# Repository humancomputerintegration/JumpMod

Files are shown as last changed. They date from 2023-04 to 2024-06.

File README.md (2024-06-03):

# JumpMod: Haptic Backpack that Modifies Users’ Perceived Jump

This is the repository for PCB schematics, Arduino code and hardware design files used to build the haptic backpack the "JumpMod: Haptic Backpack that Modifies Users’ Perceived Jump" paper (ACM CHI2023) by Romain Nith, Jacob Serfaty, Samuel Shatzkin, Alan Shen, and Pedro Lopes.

For more information, please refer to our paper: http://lab.plopes.org/#JumpMod

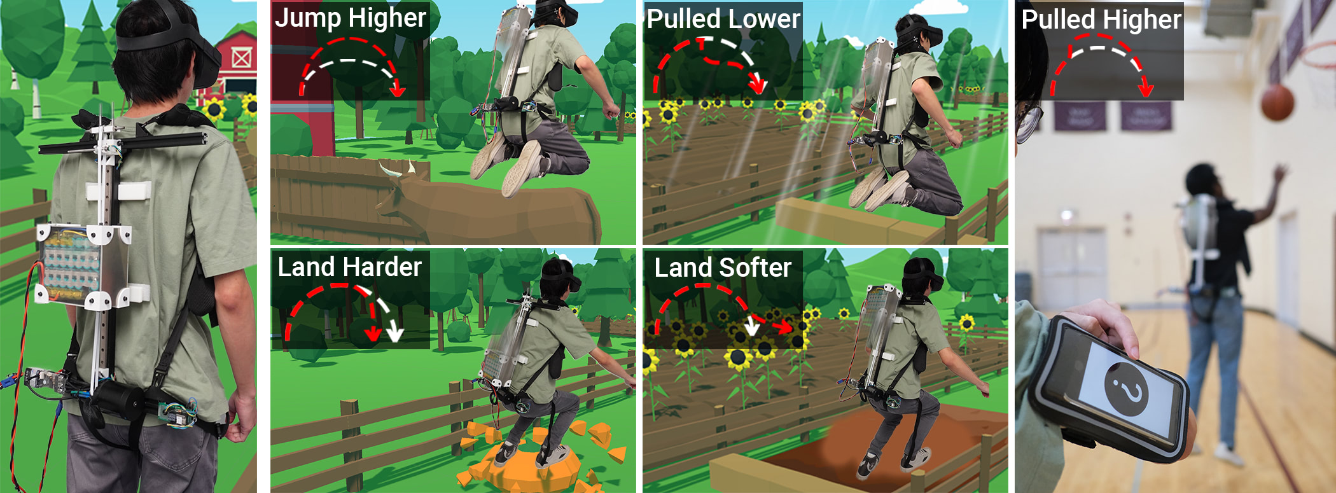
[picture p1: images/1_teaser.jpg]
1_teaser


# parts for each assembly

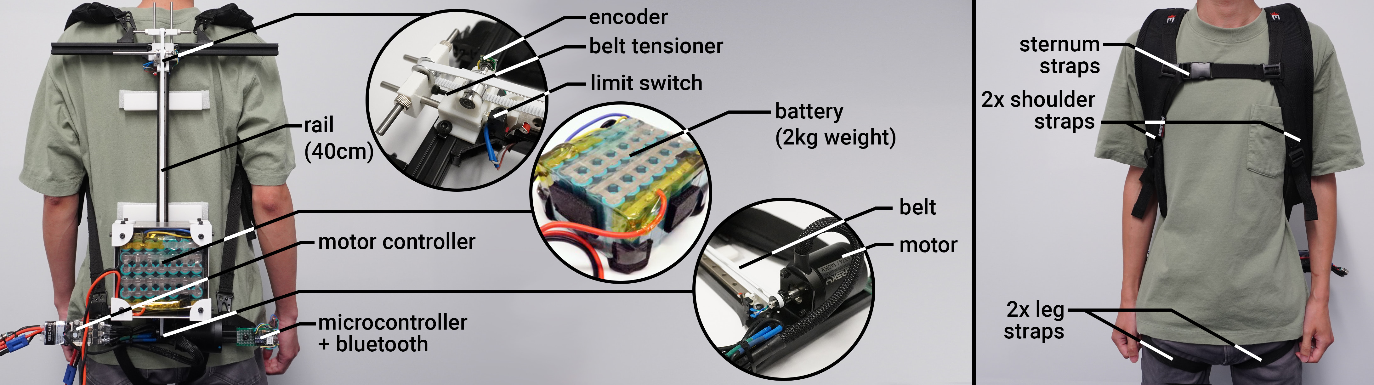
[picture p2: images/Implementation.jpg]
Implementation


| **Item** | **Qty** | **Exemplary link** | **Approx. unit cost (in USD)** |
| --- | --- | --- | --- |
| **Mechanical Frame** |
| 400mm extrusion aluminum | 2 | [Amazon link](https://www.amazon.com/gp/product/B08Y8N7FD1/ref=ppx_yo_dt_b_search_asin_title?ie=UTF8&psc=1) | 4.75 |
| 480mm extrusion aluminum | 1 | [Amazon link](https://www.amazon.com/Coavoo-Aluminum-Extrusion-Extruded-Profiles/dp/B0B4J6D1R6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) | 10.99 |
| Extrusion aluminum corner bracket | 8 | [Amazon link](https://a.co/d/40E8cxs) | 1.10 |
| M6 screws and nuts | 25 | [Amazon link](https://a.co/d/0i1jSaT) | 1.10 |
| Meister Backpack Straps | 1 | [Amazon link](https://www.amazon.com/gp/product/B077MZQ57Y/ref=ppx_yo_dt_b_search_asin_title?ie=UTF8&psc=1) | 19.99 |
| Hip straps | 2 | [Amazon link](https://www.amazon.com/Lashing-Adjustable-Tie-Down-Motorcycle-Luggage/dp/B07JRG7LJV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,aps,84&sr=8-8&th=1) | 5.00 |
| Back support | 2 | 3D printed | |
| **Belt system** |
| 2GT-6 Timing Belt with Steel Core | 1 | [Amazon link](https://www.amazon.com/gp/product/B07BDG8B1S/ref=ox_sc_act_title_3?smid=A2TMCEJ2C8SAEN&psc=1) | 9.65 |
| MGN12H 400mm Linear Rail | 1 | [Amazon link](https://www.amazon.com/gp/product/B07SL1HHSS/ref=ppx_yo_dt_b_search_asin_title?ie=UTF8&psc=1) | 25.99 |
| Micro limit switch | 2 | [Amazon link](https://www.amazon.com/gp/product/B07X142VGC/ref=ppx_yo_dt_b_search_asin_title?ie=UTF8&psc=1) | 0.59 |
| Rail limiter | 2 | 3D printed | |
| Tension system mount | 1 | 3D printed | |
| Tension system encoder mount | 1 | 3D printed | |
| Pololu Magnetic Encoder | 1 | [Pololu](https://www.pololu.com/product/3081) | 4.45 |
| M5 rod for encoder idle shaft | 1 | [Amazon link](https://www.amazon.com/gp/product/B07F3T5FKL/ref=crt_ewc_title_dp_1?ie=UTF8&psc=1&smid=AYI27JSX7SHMW) | 0.13 |
| Tension system pulley holder | 1 | 3D printed | |
| GT2 pulley for encoder idle shaft | 1 | [Amazon link](https://www.amazon.com/WINSINN-Aluminum-Synchronous-Timing-Printer/dp/B077GNZK3J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) | 1.40 |
| 100mm guiding rods for tensioning system | 3 | [Amazon link](https://www.amazon.com/gp/product/B01B27MJC6/ref=ppx_yo_dt_b_search_asin_title?ie=UTF8&psc=1) | 1.49 |
| Shaft collar for locking the rods | 2 | [Amazon link](https://www.amazon.com/Collar-Electroplate-Ferronickel-Technology-Accessories/dp/B08BZ5XS2L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) | 0.84 |
| Bearing 5mm Bore | 2 | [Amazon link](https://www.amazon.com/uxcell-605-2RS-Groove-Bearings-Double/dp/B082PR238W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) | 0.95 |
| GT2 Idler pulley | 1 | [Amazon link](https://www.amazon.com/WINSINN-Aluminum-Timing-Pulley-Printer/dp/B07BPGYX3G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) | 1.80 |
| Box adapter | 1 | 3D printed | |
| Box adapter’s belt clamp | 2 | 3D printed | |
| **Motor & motor-driver electronics** |
| Flipsky BLDC Motor 6374 140kv | 1 | [Amazon link](https://www.amazon.com/gp/product/B08G87W7WP/ref=ppx_yo_dt_b_search_asin_title?ie=UTF8&psc=1) | 119.99 |
| Flipsky FSESC V4.12 motor controller | 1 | [Amazon link](https://www.amazon.com/gp/product/B07GFB55NV/ref=ppx_yo_dt_b_search_asin_title?ie=UTF8&psc=1) | 122.99 |
| Flipsky FSESC plate mount | 1 | 2D cut | |
| Motor GT2 pulley | 1 | [Amazon link](https://www.amazon.com/GT2-Aluminum-Timing-Synchronous-Printer/dp/B08DD7BWKB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) | 1.60 |
| Motor mounting bracket | 1 | [Amazon link](https://www.amazon.com/gp/product/B07H8YQYGV/ref=ppx_yo_dt_b_search_asin_title?ie=UTF8&psc=1) | 7.99 |
| Microcontroller Seeeduino XIAO nRF52840 Sense | 1 | [Seeeduino](https://www.seeedstudio.com/Seeed-XIAO-BLE-Sense-nRF52840-p-5253.html) | 15.99 |
| **Power supply** |
| Battery<sup>1</sup> | 1 | [Amazon link](https://www.amazon.com/Lithium-Battery-20000mAh-Electric-Bicycle/dp/B08VMX8F53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) | 109.5 |
| Battery box side panel long<sup>2</sup> | 2 | 2D cut | |
| Battery box side panel short<sup>2</sup> | 2 | 2D cut | |
| Battery box top/bottom panel<sup>2</sup> | 2 | 2D cut | |
| Battery box corner bracket | 8 | 3D printed | |
| Anti-spark power switch | 1 | [Amazon link](https://www.amazon.com/DIYE-Electric-Skateboard-Anti-Spark-Longboard/dp/B07MTLV55T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,aps,80&sr=8-4) | 47.99 |

## notes
1.	Battery cells were taken from a pre-assembled battery.
2.	2mm waterjet aluminum was used to encase the battery for all sides except the top panel, which was laser cut with 3mm acrylic.

# citing
When using or building upon this device in an academic publication, please consider citing as follows:

Romain Nith, Jacob Serfaty, Samuel G Shatzkin, Alan Shen, and Pedro Lopes. 2023. JumpMod: Haptic Backpack that Modifies Users' Perceived Jump. In Proceedings of the 2023 CHI Conference on Human Factors in Computing Systems (CHI’23), April 23–28, 2023, Hamburg, Germany. ACM, NewYork,  NY, USA, 15 pages. https://doi.org/10.1145/3544548.3580764

# contact
For any questions about this repository, please contact rnith@uchicago.edu

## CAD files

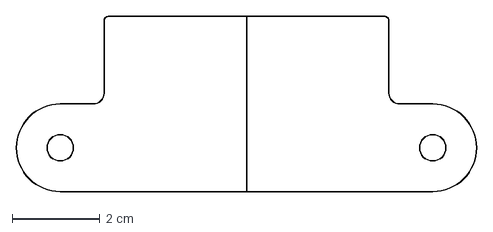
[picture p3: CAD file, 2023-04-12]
hardware/2D cuts/FSESC_plate_mount.dxf
10.5 x 4.00 cm

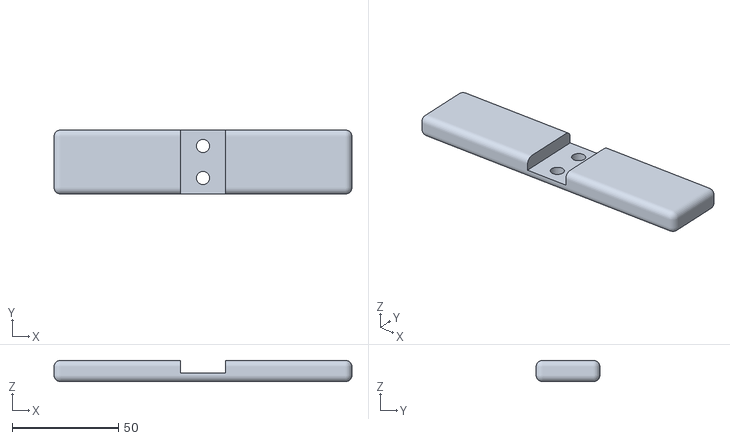
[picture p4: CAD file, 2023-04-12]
hardware/3D prints/frame-back_support.stl
140.0 x 30.0 x 10.0

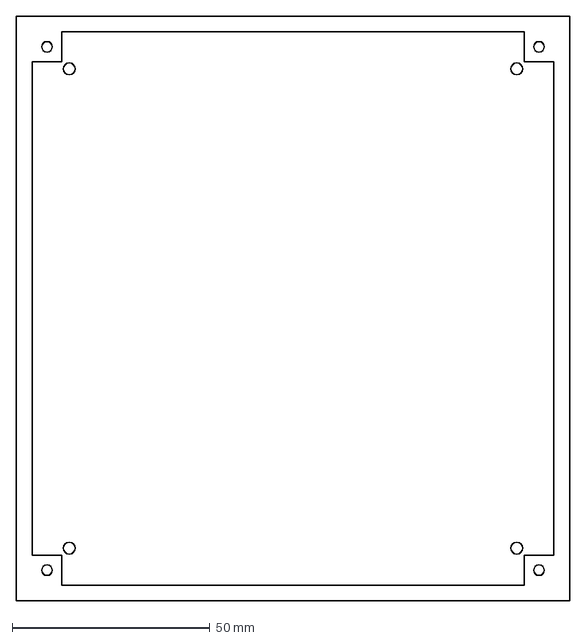
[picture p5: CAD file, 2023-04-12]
hardware/2D cuts/box-top.dxf
140.0 x 148.0 mm

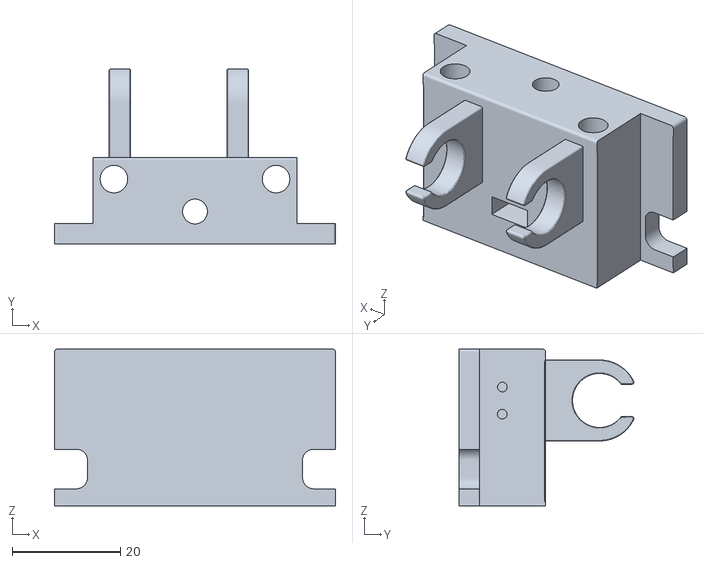
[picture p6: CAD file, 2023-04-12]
hardware/3D prints/tension-system_mount.stl
52.0 x 32.4 x 29.0

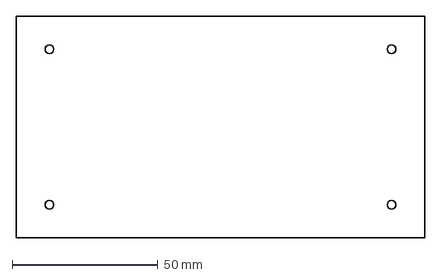
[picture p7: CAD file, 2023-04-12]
hardware/2D cuts/box-side_short.dxf
140.0 x 76.0 mm

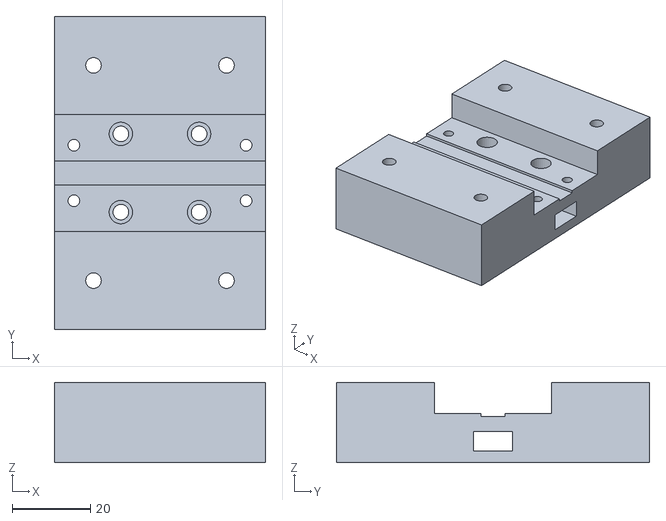
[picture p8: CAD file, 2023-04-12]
hardware/3D prints/box-adapter.stl
54.0 x 80.0 x 20.5

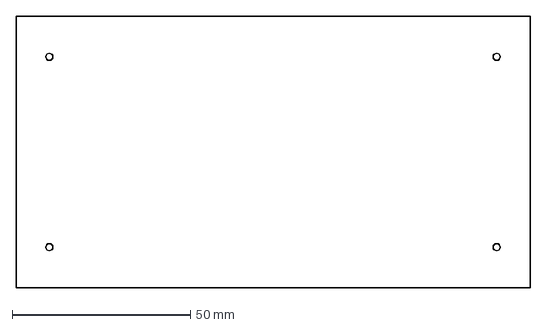
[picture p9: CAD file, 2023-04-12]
hardware/2D cuts/box-side_long.dxf
144.0 x 76.0 mm

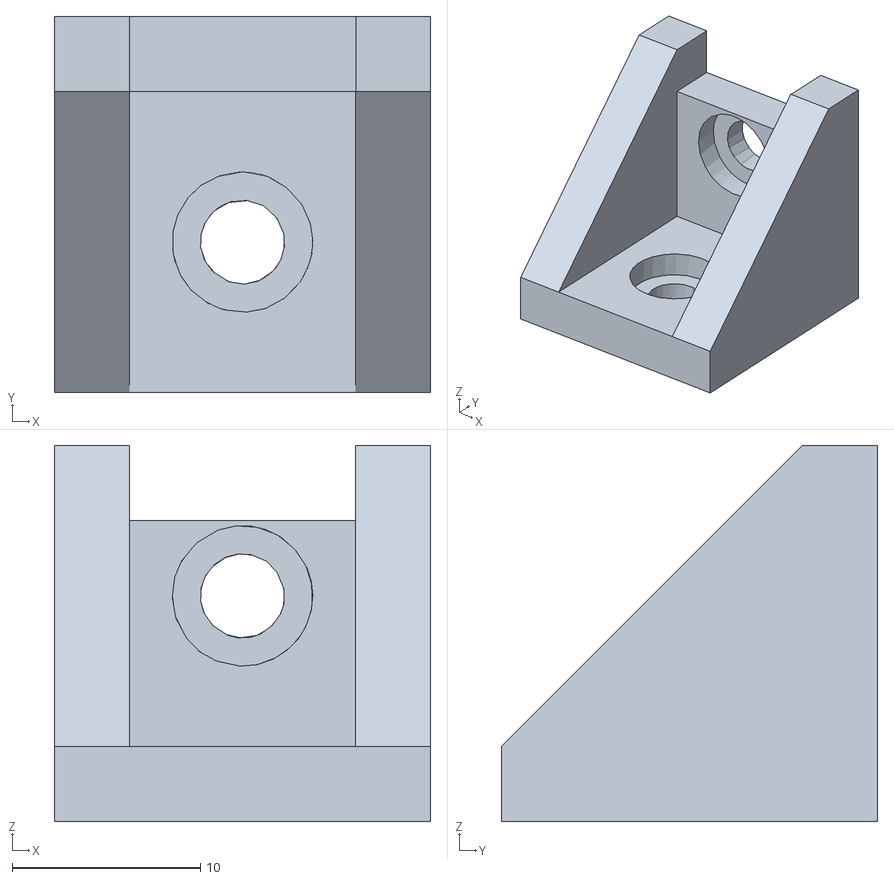
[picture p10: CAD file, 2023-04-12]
hardware/3D prints/belt-rail_limiter.stl
20.0 x 20.0 x 20.0

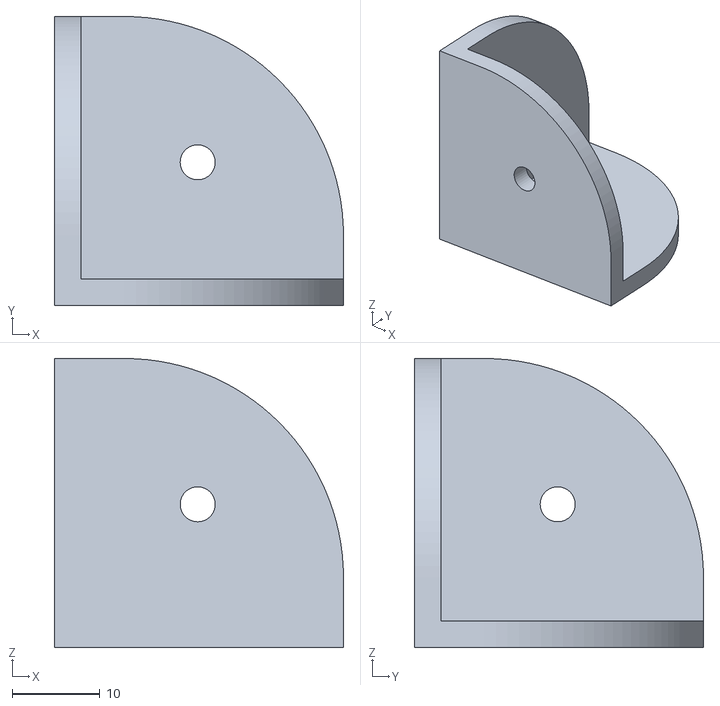
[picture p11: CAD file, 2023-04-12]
hardware/3D prints/box-corner_bracket.stl
33.0 x 33.0 x 33.0

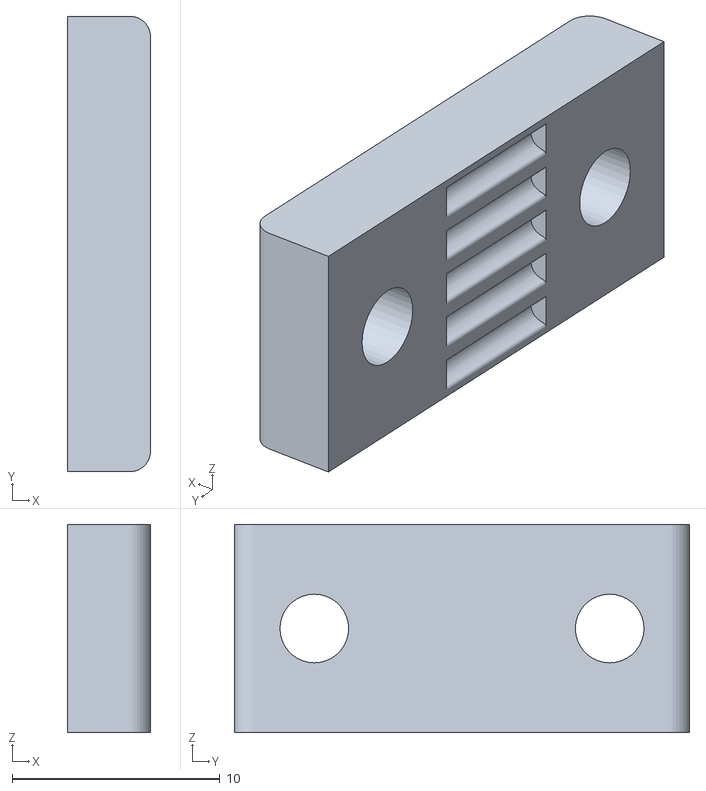
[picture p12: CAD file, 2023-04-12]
hardware/3D prints/box-adapter_belt_clamp.stl
4.00 x 21.9 x 10.0

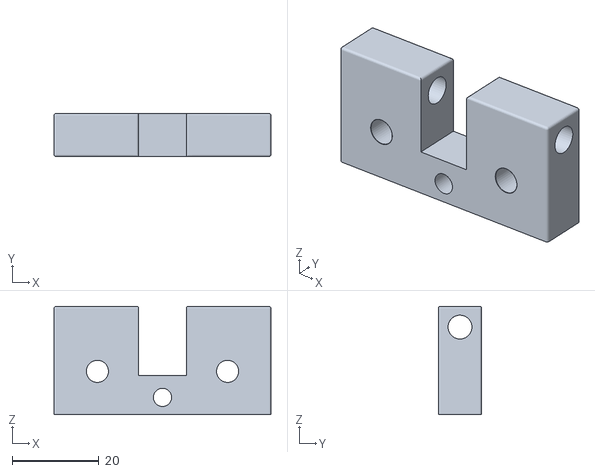
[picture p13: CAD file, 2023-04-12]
hardware/3D prints/tension-system_pulley_holder.stl
50.0 x 10.0 x 25.0

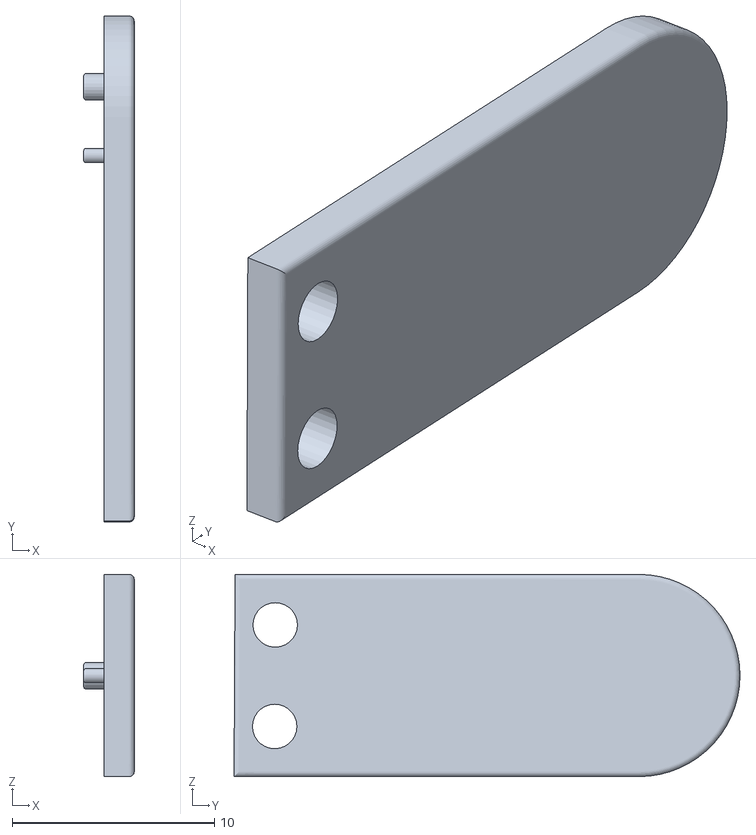
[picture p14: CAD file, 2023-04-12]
hardware/3D prints/tension-system_encoder_mount.stl
2.50 x 25.0 x 10.00

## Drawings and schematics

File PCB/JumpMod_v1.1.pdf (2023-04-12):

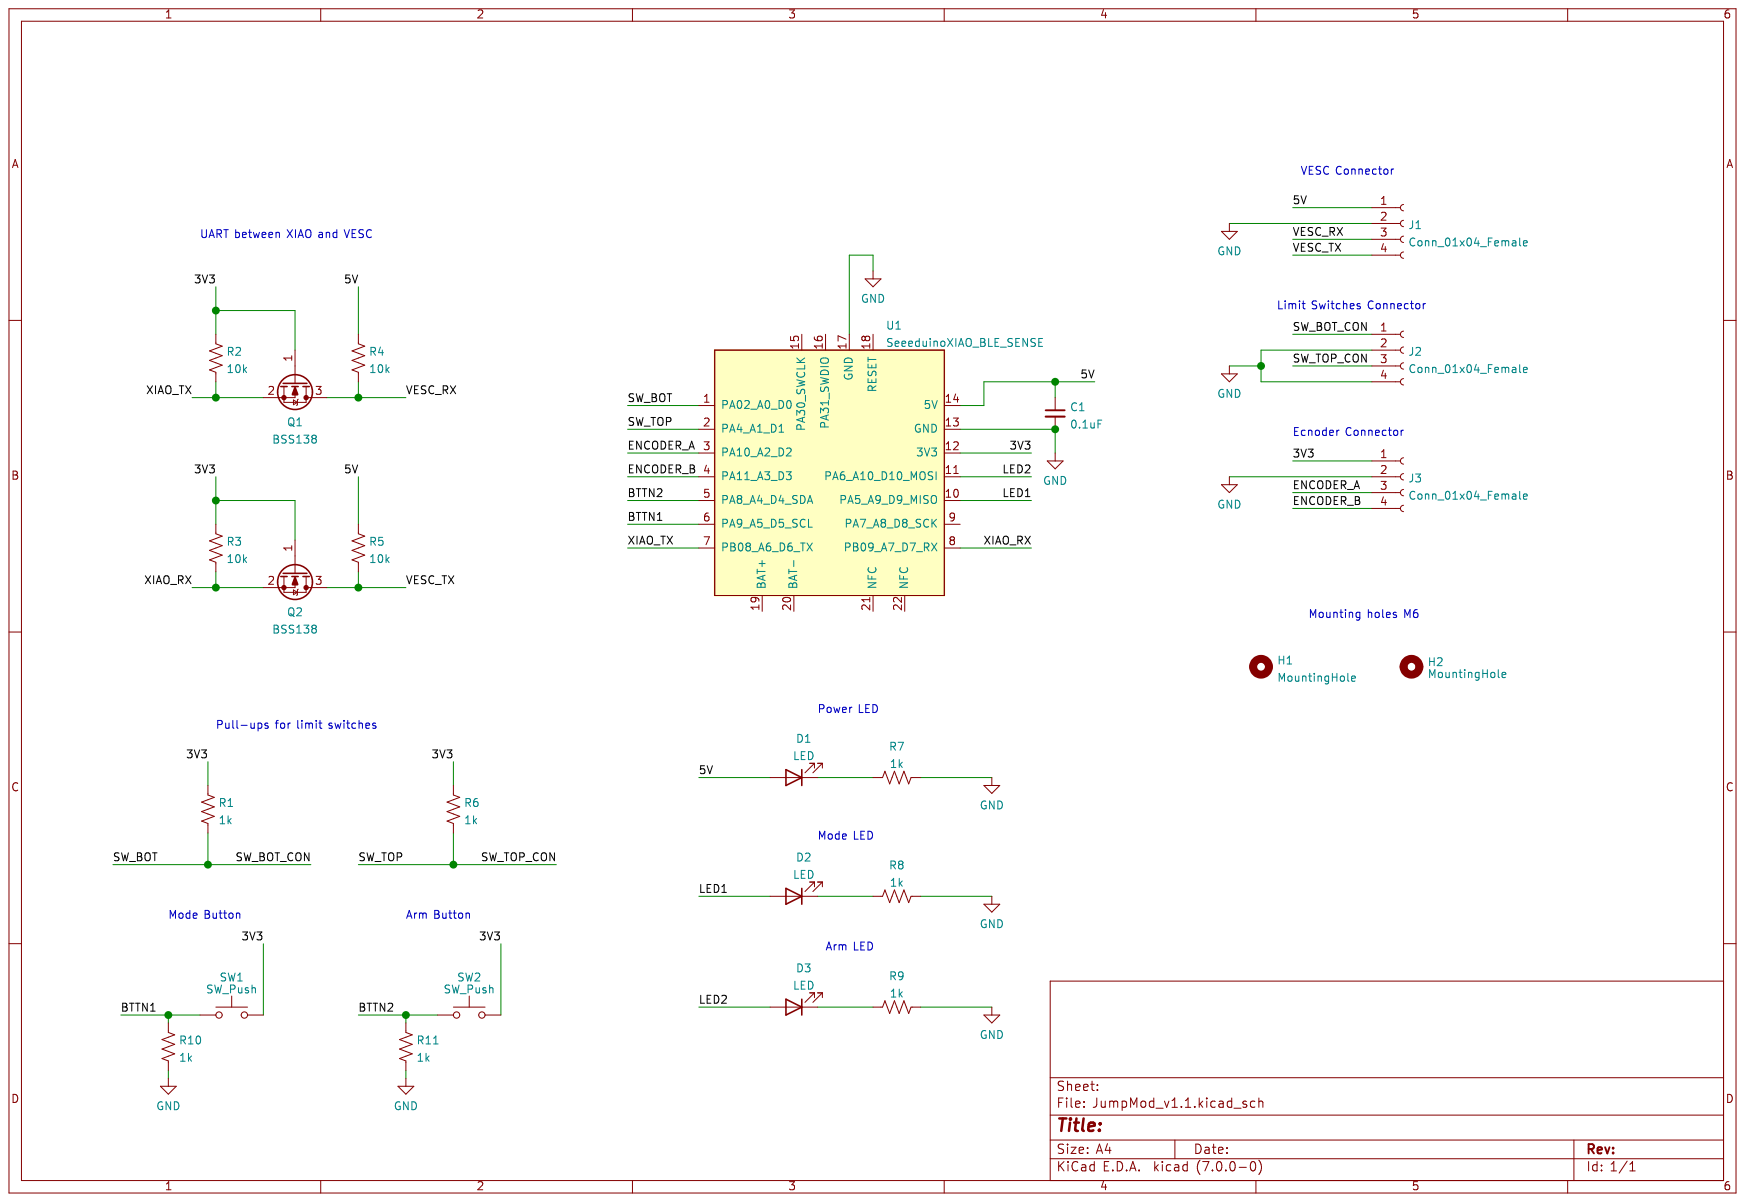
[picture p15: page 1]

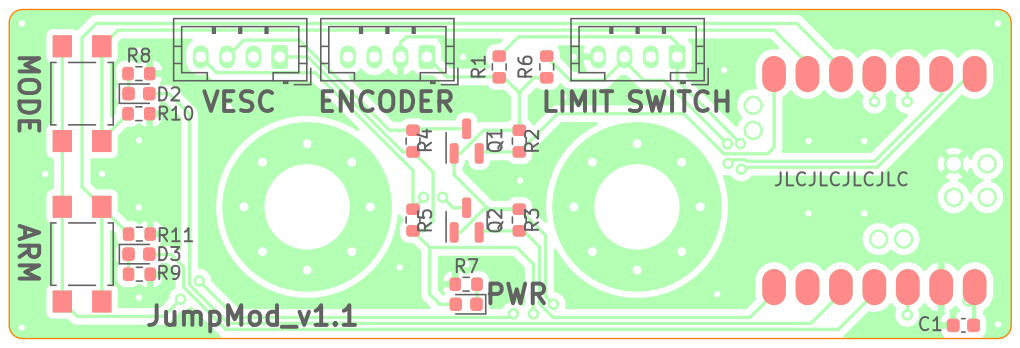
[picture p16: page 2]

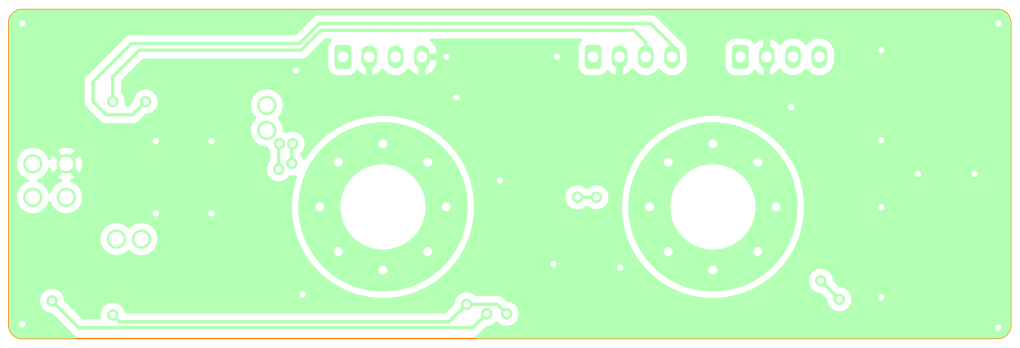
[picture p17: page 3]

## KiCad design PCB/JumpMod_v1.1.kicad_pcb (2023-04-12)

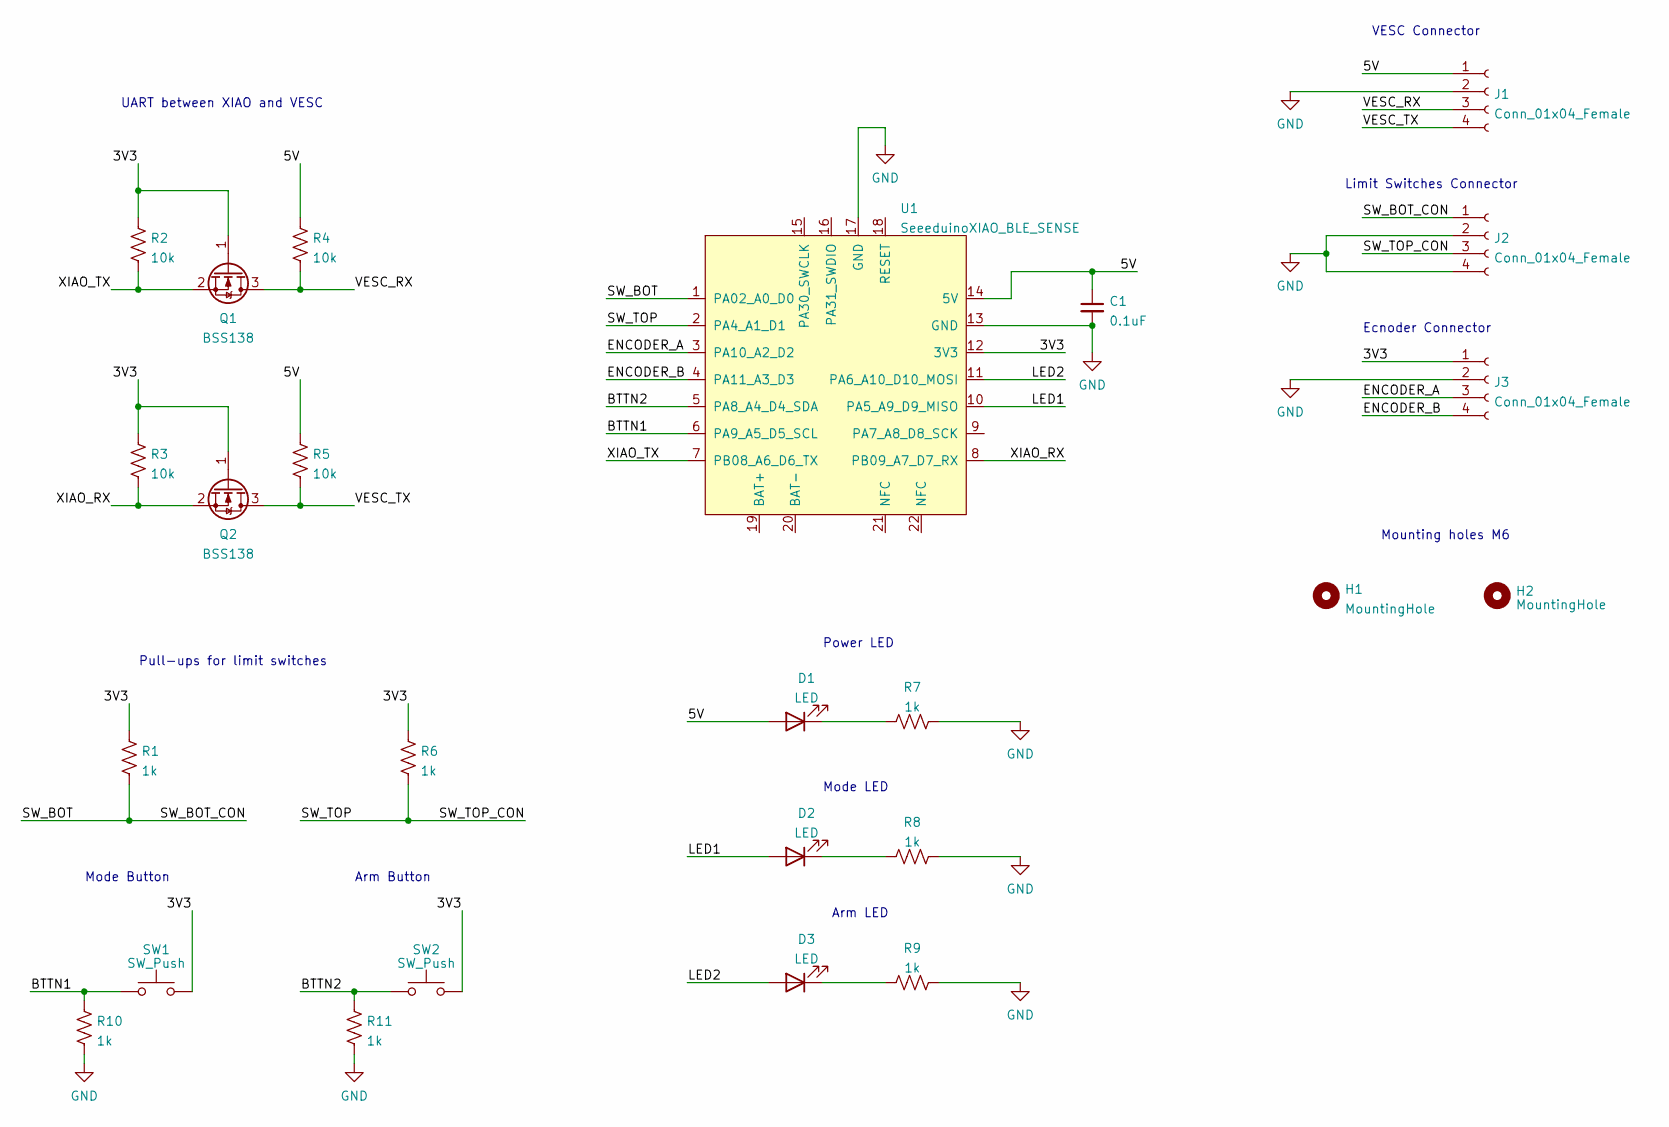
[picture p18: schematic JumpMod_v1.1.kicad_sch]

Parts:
C1: 0.1uF; C_0603_1608Metric
D1, D2, D3: LED; LED_0603_1608Metric
H1, H2: MountingHole; MountingHole_6.4mm_M6_Pad_Via
J1, J2, J3: Conn_01x04_Female; JST_PH_B4B-PH-K_1x04_P2.00mm_Vertical
Q1, Q2: BSS138; SOT-23
R1, R6, R7, R8, R9, R10, R11: 1k; R_0603_1608Metric
R2, R3, R4, R5: 10k; R_0603_1608Metric
SW1, SW2: SW_Push; SW_SPST_TL3305B
U1: SeeeduinoXIAO_BLE_SENSE; xiao-ble-smd

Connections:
/3V3: J3.1, Q1.1 (G), Q2.1 (G), R1.1, R2.1, R3.1, R6.1, SW1.2, SW2.2, U1.12 (3V3)
/5V: C1.1, D1.2 (A), J1.1, R4.1, R5.1, U1.14 (5V)
/BTTN1: R10.1, SW1.1, U1.6 (PA9_A5_D5_SCL)
/BTTN2: R11.1, SW2.1, U1.5 (PA8_A4_D4_SDA)
/ENCODER_A: J3.3, U1.3 (PA10_A2_D2)
/ENCODER_B: J3.4, U1.4 (PA11_A3_D3)
/LED1: D2.2 (A), U1.10 (PA5_A9_D9_MISO)
/LED2: D3.2 (A), U1.11 (PA6_A10_D10_MOSI)
/SW_BOT: J2.1, R1.2, U1.1 (PA02_A0_D0)
/SW_TOP: J2.3, R6.2, U1.2 (PA4_A1_D1)
/VESC_RX: J1.3, Q1.3 (D), R4.2
/VESC_TX: J1.4, Q2.3 (D), R5.2
/XIAO_RX: Q2.2 (S), R3.2, U1.8 (PB09_A7_D7_RX)
/XIAO_TX: Q1.2 (S), R2.2, U1.7 (PB08_A6_D6_TX)
GND: C1.2, J1.2, J2.2, J2.4, J3.2, R7.2, R8.2, R9.2, R10.2, R11.2, U1.13 (GND), U1.17 (GND)
unnamed: D1.1 (K), R7.1
unnamed: D2.1 (K), R8.1
unnamed: D3.1 (K), R9.1

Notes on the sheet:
Mounting holes M6
Mode LED
Arm Button
Mode Button
Ecnoder Connector
Power LED
VESC Connector
Limit Switches Connector
Arm LED
UART between XIAO and VESC
Pull-ups for limit switches

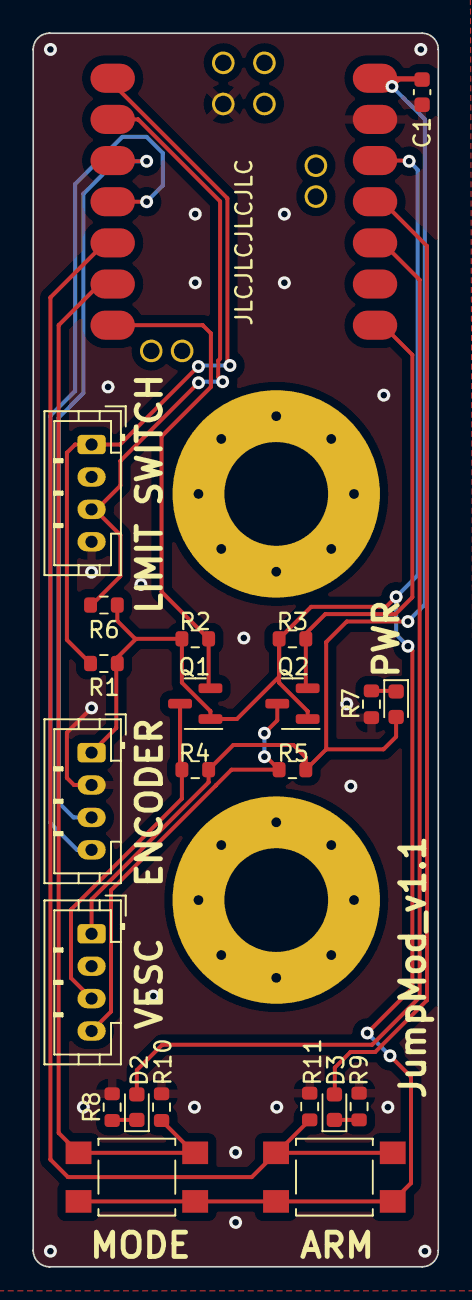
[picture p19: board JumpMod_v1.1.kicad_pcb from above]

Board: 2 copper layers, 25.0 x 76.1 mm, 25 parts (0 on the bottom side), 18 nets.

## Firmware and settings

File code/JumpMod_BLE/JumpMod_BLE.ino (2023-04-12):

/*
    JumpMod_BLE -- firmaware for JumpMod haptic backpack
    built for Seeeduino XIAO nRF52840 Sense with Arduino
*/

#include "JumpController.h"
#include "LSM6DS3.h"
#include "Wire.h"
#include <ArduinoBLE.h>
#include <SimpleFOC.h> // https://docs.simplefoc.com/low_pass_filter

#define SERVICE_UUID        "4fafc201-1fb5-459e-8fcc-c5c9c331914b"
#define GET_CHARACTERISTIC_UUID "beb5483e-36e1-4688-b7f5-ea07361b26a8"
#define SEND_CHARACTERISTIC_UUID "8628FE7C-A4E9-4056-91BD-FD6AA7817E39"
#define TRIGGER_CHARACTERISTIC_UUID "1fee8942-0f64-11ed-861d-0242ac120002"
#define VOLTAGE_CHARACTERISTIC_UUID "9c5a211f-d400-490b-9465-52f7a417d19c"
#define POSITION_CHARACTERISITC_UUID "3deefe33-d8f5-45a8-a24c-8fec01486b03"

JumpController myJC;

//Create a instance of class LSM6DS3
LSM6DS3 xiaoIMU(I2C_MODE, 0x6A);    //I2C device address 0x6A

/* XIAO BLE Sense Params */
float accX = 0.0F;
float accY = 0.0F;
float accZ = 0.0F;

unsigned long prevdt = 0;
bool isUpsideDown = false;

/* Communication Params */
boolean newData = false;
const byte numChars = 32;//11;
char receivedChars[numChars];
char tempChars[numChars];        // temporary array for use when parsing


BLEService jumpService(SERVICE_UUID); // Bluetooth® Low Energy LED Service
// Bluetooth® Low Energy LED Switch Characteristic - custom 128-bit UUID, read and writable by central
BLECharacteristic jumpCharacteristic(GET_CHARACTERISTIC_UUID, BLERead | BLEWrite, "           "); // Sets max size to 11 with a 11 length string
BLECharacteristic sendCharacteristic(SEND_CHARACTERISTIC_UUID, BLERead | BLEWrite | BLENotify, " "); // Sets max size to 1 with a 1 length string
BLEByteCharacteristic triggerCharacteristic(TRIGGER_CHARACTERISTIC_UUID, BLERead | BLEWrite | BLENotify); // Should only contain either 0 or 1
BLECharacteristic voltageCharacteristic(VOLTAGE_CHARACTERISTIC_UUID, BLERead | BLENotify, "     "); // Battery voltage, 5 characters, ie "22.50"
BLECharacteristic positionCharacteristic(POSITION_CHARACTERISITC_UUID, BLERead | BLENotify, "   "); // Encoder position, 3 ~char

bool isConnected = false;

// Blinks the LED every 100 interations to show the code is running
int blinkCounter = 0;

int oscEvalTimer = 0;
bool alreadyLogged = false;
int logVal = 0;

LowPassFilter filter = LowPassFilter(0.01);

unsigned long lastVoltageRead;
int prevSentPosition = -100; // Throwaway value so it sends on startup

void setup() {
  xiaoIMU.begin();

  myJC.onlyPrediction = false;
  myJC.setup();

  // Setup BLE
  if (!BLE.begin()) {
    Serial.println("starting Bluetooth® Low Energy module failed!");
    while (1);
  }

  // set advertised local name and service UUID:
  BLE.setLocalName("Jumper"); 
  BLE.setAdvertisedService(jumpService);

  // add the characteristic to the service
  jumpService.addCharacteristic(jumpCharacteristic);
  jumpService.addCharacteristic(sendCharacteristic);
  jumpService.addCharacteristic(triggerCharacteristic);
  jumpService.addCharacteristic(voltageCharacteristic);
  jumpService.addCharacteristic(positionCharacteristic);

  // add service
  BLE.addService(jumpService);

  // start advertising
  BLE.advertise();

  //Setup LED
  pinMode(LED_BUILTIN, OUTPUT);
}

void readCommand() {
  const unsigned char *value = jumpCharacteristic.value();
  strcpy(tempChars, (const char*) value);
  if (tempChars[0] == 'l') {
    digitalWrite(LED_BUILTIN, LOW);
    myJC.lightCommandOn = true;
  }
  myJC.parseData(tempChars);
  if (myJC.debug && !myJC.debugPlot) {
    Serial.print("Message received: ");
    Serial.println((const char*) value);
  }
}

void readTrigger() {
  byte incoming = 0;
  triggerCharacteristic.readValue(incoming);
  if (incoming == '1') {
    triggerCharacteristic.writeValue('0');
    myJC.trigger();
    myJC.lightCommandOn;
  }
  else if (incoming == '0') {
    myJC.resetQueue();
  }
}

void loop() {
  // get position from encoder
  myJC.getPosition();

  if (!myJC.predictJump){
    myJC.driveController();

    myJC.currentTime = millis();
    if (myJC.driveStatus == "initial") {
      myJC.drivePosition();
    }
    myJC.previousTime = myJC.currentTime; 
  }
 
  // /* Handle commands */
  if (myJC.drive) {
    recvWithStartEndMarkers();
    if (newData == true) {
      strcpy(tempChars, receivedChars);
      // this temporary copy is necessary to protect the original data
      //   because strtok() used in parseData() replaces the commas with \0
      if (tempChars[0] == 'l') {
        digitalWrite(LED_BUILTIN, LOW);
        myJC.lightCommandOn = true;
      }
      else if (tempChars[0] == 'o') {
        oscEvalTimer = 200;
        Serial.println("Sending \"0\" to OSC/command");
        digitalWrite(LED_BUILTIN, LOW);
        myJC.lightCommandOn = true;
      }
      myJC.parseData(tempChars);
      newData = false;
    }
  }

  if(myJC.queuedMovements.empty()) {
    if(myJC.vibrationMode == 1) {
      myJC.addQueue(myJC.vibrateDC, 30);
      myJC.addQueue(myJC.vibrateDC, 70);
    }
    else if(myJC.vibrationMode == 4) {
      myJC.addQueue(myJC.vibrateSoftDC, myJC.vibrationOffset);
      myJC.addQueue(myJC.vibrateSoftDC, myJC.vibrationPosition);
      Serial.print("Queuing: " + String(myJC.vibrateSoftDC) + " - " + String(myJC.vibrationOffset));
      Serial.println(" and: " + String(myJC.vibrationPosition) + " current: " + String(myJC.encoderPosition));
    }
    else {
      myJC.vibrationMode = 0;
    }
  }
  // vibrate regular
  if (myJC.vibrationMode != 0 && (myJC.driveStatus == "brake" || myJC.driveStatus == "none")
      && !myJC.queuedMovements.empty() ) {
    
    myJC.trigger();
  }

  

  /* BLE */
  bool connected = BLE.connected();
  if (connected && !isConnected) {
    isConnected = true;
    if (myJC.debug && !myJC.debugPlot) {
      Serial.println("Bluetooth device connected!");
    }
  }
  else if (!connected && isConnected) {
    isConnected = false;
    BLE.advertise();
    if (myJC.debug && !myJC.debugPlot) {
      Serial.println("Bluetooth device disconnected! Restarting advertising...");
    }
  }

  /* Read bluetooth messages */
  if (jumpCharacteristic.written()) {
    blinkCounter = 0;
    digitalWrite(LED_BUILTIN, LOW);
    readCommand();
  }
  /* Blink the LED */
  controlLED();

  if (triggerCharacteristic.written()) {
    readTrigger();
  }

  /* Call jump prediction functions when enabled */
  if (myJC.predictJump) {
    predictJump();
  }

  if (millis() - lastVoltageRead > 2000 && myJC.UART.getVescValues()) {
    lastVoltageRead = millis();
    myJC.batteryVoltage = myJC.UART.data.inpVoltage;
    voltageCharacteristic.writeValue(String(myJC.batteryVoltage).c_str());
  }

  if (prevSentPosition != myJC.encoderPosition ) {
    positionCharacteristic.setValue(String((myJC.encoderPosition * 100) / myJC.encoderTopPosition).c_str());
    prevSentPosition = myJC.encoderPosition;
    if(myJC.debug && !myJC.debugPlot && myJC.debugBLE) {
      Serial.println("Sent via BLE: Position = " + String((myJC.encoderPosition * 100) / myJC.encoderTopPosition));
    }
  }
}

void controlLED() {
  if (myJC.lightCommandOn) {
    blinkCounter = 0;
    myJC.lightCommandOn = false;
  }
  if (blinkCounter == 1000) {
    digitalWrite(LED_BUILTIN, HIGH);
  }
  if (blinkCounter == 0) {
    digitalWrite(LED_BUILTIN, LOW);
  }
  blinkCounter = (blinkCounter + 1) % 2000;
  if (blinkCounter >= 1001 && myJC.useBlinkCommands) {
    blinkCounter = 1001;
  }
}

void predictJump() {
  /* Jump prediction setup */
  // Read acceleration values
  accX = xiaoIMU.readFloatAccelX();
  accY = xiaoIMU.readFloatAccelY();
  accZ = xiaoIMU.readFloatAccelZ();
  accX *= 9.8 * 9.8 / 9.93;
  accY *= 9.8 * 9.8 / 9.93;
  accZ *= 9.8 * 9.8 / 9.93;

  // Apply a low-pass filter on the accelation data to reduce noise
  float YZ = filter(sqrt(sq(accY) + sq(accZ))) - 9.8;
  if (isUpsideDown) {
    YZ *= -1;
  }
  myJC.loop(YZ);

  // Print plotting info
  if (myJC.debugPlot && !alreadyLogged && logVal == 0) {
    unsigned long dt = millis();
    unsigned long deltaTime = dt - prevdt;
    prevdt = dt;
    Serial.print(
      "YZ: " + String(YZ) +
      ", Velocity: " + String(myJC.velocity) + ", Displacement: " + String(myJC.displacement * 5) +
      ", Jump Status: " + String((float)(myJC.jumpStatus - 1) / (float) 4));
    if (myJC.jumpStatus == 9 && !alreadyLogged) {
      alreadyLogged = true;
    }
    if (myJC.maxAccel != -9999) {
      Serial.print(", Max accel: " + String(myJC.maxAccel));
    }
    Serial.println(myJC.printDT ? (" Delta Time: " + String(deltaTime)) : "");
  }
  logVal = (logVal + 1) % 5;

  int sendCharValue = atoi((const char *) sendCharacteristic.value());

  if (oscEvalTimer > 0) {
    if (isConnected && oscEvalTimer == 200) {
      sendCharacteristic.writeValue("0");
    }
    oscEvalTimer--;
    return;
  }
  // Ensure the user is not tilted on the Z-axis
  else if (abs(myJC.displacement) > 4) {
    if (myJC.debug && !myJC.debugPlot) {
      Serial.println("Error: You are not rotated correctly!");
    }
    if (isConnected && sendCharValue > 0) {
      sendCharacteristic.writeValue("0");
    }
  }
  else if (isConnected && sendCharValue <= 0) {
    sendCharacteristic.writeValue((char *) String((int) myJC.jumpStatus).c_str());
    if (myJC.debug && !myJC.debugPlot) {
      Serial.println("Sent via BLE: " + String(myJC.jumpStatus));
    }
  }
  sendCharValue = atoi((const char *) sendCharacteristic.value());
  /* Update bluetooth jump status */
  if (isConnected && sendCharValue != (int) myJC.jumpStatus && sendCharValue > 0) {
    sendCharacteristic.writeValue((char *) String((int) myJC.jumpStatus).c_str());
    if (myJC.debug && !myJC.debugPlot) {
      Serial.println("Sent via BLE: " + String(myJC.jumpStatus));
    }
  }
}

// Read data from the Serial monitor
void recvWithStartEndMarkers() {
  static boolean recvInProgress = false;
  static byte ndx = 0;
  char startMarker = '<';
  char endMarker = '>';
  char rc;

  while (Serial.available() > 0 && newData == false) {
    rc = Serial.read();

    if (recvInProgress == true) {
      if (rc != endMarker) {
        receivedChars[ndx] = rc;
        ndx++;
        if (ndx >= numChars) {
          ndx = numChars - 1;
        }
      }
      else {
        receivedChars[ndx] = '\0'; // terminate the string
        recvInProgress = false;
        ndx = 0;
        newData = true;
      }
    }

    else if (rc == startMarker) {
      recvInProgress = true;
    }
  }
}

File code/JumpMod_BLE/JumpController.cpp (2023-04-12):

/*
    JumpController.h -- firmaware for JumpMod haptic backpack
    built for Seeeduino XIAO nRF52840 Sense with Arduino
*/

#include "JumpController.h"
#include <Arduino.h>
#include <Adafruit_MPU6050.h>
#include <Adafruit_Sensor.h>
#include <VescUart.h>
#include <math.h>


#define SWITCH_BOT 0 // limit switch bottom
#define SWITCH_TOP 1 // limit switch top
#define ENCODER_A 2
#define ENCODER_B 3

#define readA digitalRead(ENCODER_A)  //bitRead(PIND,2) // faster than digitalRead() -- doesnt work
#define readB digitalRead(ENCODER_B)  //bitRead(PIND,3) // faster than digitalRead()

int count = 0; // used by interrupts to count encoder

void JumpController::setup() {
  /** Setup serial port for computer com **/
  Serial.begin(115200);
  Serial.println("JumpAR program begins...");

  if (!onlyPrediction) {
    /** Setup UART port for VESC (Serial1 on Atmega32u4) */
    Serial1.begin(115200);

    /** Define which ports to use as UART */
    UART.setSerialPort(&Serial1);

    Serial.println("UART initialization successful!");

    pinMode(SWITCH_BOT, INPUT);
    pinMode(SWITCH_TOP, INPUT);

    pinMode(ENCODER_A, INPUT_PULLUP);
    pinMode(ENCODER_B, INPUT_PULLUP);

    attachInterrupt(digitalPinToInterrupt(ENCODER_A), isrA, CHANGE);
    attachInterrupt(digitalPinToInterrupt(ENCODER_B), isrB, CHANGE);    
    
  }
}

void JumpController::loop(float YZ) { // used with prediction
  // Predict user's jump status every 10ms
  predictJumpStatus(YZ);

  if (!onlyPrediction) {
    // Perform powered jump if we are in powered jump mode and the user jumps
    if (jumpStatus == predStartDrive && powerJumpPhase == "none" && powerJump) { // condition to start drive
      startJump(powerJumpDutyCycle, powerJumpDriveDuration);
      powerJumpPhase = "up";
    }
    else if (jumpStatus == predStopDrive && powerJumpPhase == "up" && driveStatus == "initial" && powerJump) // condition to stop drive
    {
      driveStatus = "brake";
      if (debug && !debugPlot) {
        Serial.println("Apex reached, stopping drive early");
      }
    }
    else if (jumpStatus == 1 && powerJumpPhase == "up") { // condition to reset weight
      if (powerJumpDutyCycle < 0)
        startJump(.05, 4000);
      else if (powerJumpDutyCycle > 0)
        startJump(-.05, 4000);
      powerJumpPhase = "down";
    }
    else if (powerJumpPhase == "down" && driveStatus == "none")
    {
      powerJumpPhase = "none";
    }

    if (drive) {
      driveMotor();
    }
  }

  if (millis() - lastPrint > 500) {
    lastPrint = millis();
    // pinging the ESC
    if (!onlyPrediction)
      if (driveStatus == "none")
        UART.setDuty(0);
  }

  // debug limit switches
  if (debugSW && !debugPlot) {
    Serial.print("SW_B = ");
    Serial.print(digitalRead(SWITCH_BOT));
    Serial.print(" -- ");
    Serial.print("SW_T = ");
    Serial.println(digitalRead(SWITCH_TOP));

  }
}

void JumpController::driveController(){ // used with without prediction
  if (millis() - lastPrint > 500) {
    lastPrint = millis();
    // pinging the ESC
    if (!onlyPrediction)
      if (driveStatus == "none")
        UART.setDuty(0);
  }

//  // brake if switch hit and driving
//  if ( (digitalRead(SWITCH_TOP) == 1 || digitalRead(SWITCH_BOT) == 1) 
//    && (driveStatus != "brake" || driveStatus != "none" ) ) {
//    driveStatus = "brake"; 
//    UART.setDuty(0);
//  }
  
  // debug limit switches
  if (debugSW && !debugPlot) {
    Serial.print("SW_B = ");
    Serial.print(digitalRead(SWITCH_BOT));
    Serial.print(" -- ");
    Serial.print("SW_T = ");
    Serial.println(digitalRead(SWITCH_TOP));
  }
}

void JumpController::isrA() {
  if(readB != readA) {
    count ++;
  } else {
    count --;
  }
}
void JumpController::isrB() {
  if (readA == readB) {
    count ++;
  } else {
    count --;
  }
}

void JumpController::getPosition() {
  noInterrupts();
  encoderPosition = count;
  interrupts();
  
  if (debug && debugPosition) {
    if (encoderPrevPosition != encoderPosition) {
      Serial.println("Position: " + String(encoderPosition) + " - " + String((encoderPosition*100)/encoderTopPosition));    
    }
  }
  encoderPrevPosition = encoderPosition;
}

void JumpController::encoderCalibration() {
  // Make sure the weight is at the bottome
  while (digitalRead(SWITCH_BOT) != 1)  UART.setDuty(0.05);
  count = 0;
  
  while (digitalRead(SWITCH_TOP) != 1)  {
    UART.setDuty(-0.05);
    getPosition();
  }
  encoderTopPosition = count;
  while (digitalRead(SWITCH_BOT) != 1)  UART.setDuty(0.1);
  calibRoutine = false;  
  Serial.println("Calibration done, new value: " + String(encoderTopPosition));
}

void JumpController::drivePosition() {
  if (encoderPosition > targetPosition && dutyCycle > 0 && driveStatus != "brake") { // driving downwards, positive dutyCycle
  // limit switch when driving down
    if (digitalRead(SWITCH_BOT) == 1) {
        driveStatus = "brake"; 
        count = 0;
    }
  }
  else if (encoderPosition < targetPosition && dutyCycle < 0 && driveStatus != "brake") { // driving upwards, positive dutyCycle
    // limit switch when driving up
    if (digitalRead(SWITCH_TOP) == 1) {        
        driveStatus = "brake"; 
        if (!calibRoutine) count = encoderTopPosition;
     }
  }
  else {
    driveStatus = "brake";
  }

  dutyCycle_PID = - computePID(encoderPosition); // flip PID sign
  if (debug && !debugPlot && debugPID) {
    Serial.print("PID output " + String(dutyCycle_PID));
    Serial.print(" kp " + String(kp * errorToTarget));
    Serial.print(" ki " + String(ki * cumError));
    Serial.print(" kd " + String(kd * rateError));
  }
  // clamping duty cycle or is vibrating
  if (abs(dutyCycle_PID) > abs(dutyCycle) || vibrationMode > 0) {
    dutyCycle_PID = dutyCycle;
  }
  
  if (debug && !debugPlot && debugPID) Serial.println(" PID output clamped " + String(dutyCycle_PID));

  // send message every 900ms so it doesn't fill up ESC buffer
  if (driveStatus != "brake") {
    if (millis() - timePrev >= 900 || firstDrive == 0 || dutyCycle_PID != prevDutyCycle_PID) { 
      if (drive) UART.setDuty(dutyCycle_PID);
      firstDrive = 1;
      timePrev = millis();
    }
  }
  else {
    driveStatus = "brake";
  }

  prevDutyCycle_PID = dutyCycle_PID;
  
  if (driveStatus == "brake") {
    firstDrive == 0;
    if (drive) {
      UART.setDuty(0);
      driveStatus = "none";
    }
  }
}
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

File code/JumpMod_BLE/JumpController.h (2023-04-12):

/*
    JumpController.h -- firmaware for JumpMod haptic backpack
    built for Seeeduino XIAO nRF52840 Sense with Arduino
*/

#ifndef JumpController_h
#define JumpController_h
#include <Arduino.h>
#include <Adafruit_MPU6050.h>
#include <Adafruit_Sensor.h>
#include <VescUart.h>
#include <Wire.h>
#include <math.h>
#include <Queue.h>
#include <utility>

class JumpController
{
  public:
    // Functions
    void loop(float YZ);
    void driveController();
    void parseData(char* tempChars);
    void getPosition();
    void encoderCalibration();
    void driveMotor();
    void drivePosition();
    double computePID(int input);
    void startJump(float newDutyCycle, int newTimeInMS);
    void setup();
    void predictJumpStatus(float YZ);
    void printJumpStatus();
    void trigger();
    void addQueue(float dutyCycle, int targetPos);
    void resetQueue();
    int countToPercentage(int positionCount);
    int percentageToCount(int positionPercentage);

    // Settings
    bool debug = false; // Frequently prints data
    bool useBlinkCommands = true; // Disables regular light blinking so BLE can manually trigger blinking
    bool predictJump = false; // Runs the jump prediction algorithm and uses it to control the motor

    bool debugPlot = false; // Prints only acceleration, displacement, and velocity in serial-plotter-readable format
    bool printDT = false;
    bool debugSW = false;
    bool debugPredict = false;
    bool debugPosition = true;
    bool debugBLE = false;
    bool debugPID = false;

    bool drive = true;
    bool onlyPrediction = false;
    bool calibRoutine = false;

    // Trigger queing controls
    std::queue<std::pair<float, int>> queuedMovements;


    // driving variables
    float dutyCycle = 0;
    float dutyCycle_PID = 0;
    float prevDutyCycle_PID = 0;
    int targetPosition = 0;
    int timeinms = 0;
    int predStartDrive = 3;
    int predStopDrive = 4;
    float batteryVoltage = 0;
    int vibrationMode = 0; // 0 = none, 1 = vibrate regular, 2 = vibrate up, 3 = vibrate down
    float vibrateDC = 0.15f;
    float vibrateSoftDC = 0.05f;
    int vibrationPosition = 0;
    int vibrationOffset = 0;
    
    // encoder position
    int encoderPosition = 0;
    int encoderPrevPosition;
    int encoderTopPosition = 101; // tune this accordingly or run calibRouting()  
    bool encoderReset = false;  // avoid race condition when reseting encoder value at each end

    // PID variables
    double kp = 0.007;
    double ki = 0.000001;
    double kd = 0.1;
    
    unsigned long currentTime, previousTime;
    double elapsedTime;
    double errorToTarget;
    double lastError;
    double input, output;
    double cumError, rateError;
    
    // Timer
    unsigned long timeZero, timePrev;
    unsigned long timeAtTarget;
    unsigned long prevLoopTime = 0;

    // Jump Status
    enum JumpStatus {
      STAND = 1,
      CROUCH,
      LAUNCH,
      LIFTOFF,
      ASCENT,
      APEX,
      DESCENT,
      LANDING,
      REBOUND
    };
    JumpStatus jumpStatus = STAND;
    int statusStart = 0;

    // Callibration
    int sameCount = 0;
    int sameCountMax = 3; // Reset to 0 velocity when sameCount reaches this value
    float launchDetectionConstant = -0.3;
    float crouchBound = -0.3;
    float liftoffDetectionFactor = 0.8; // When acceleration goes below this factor of maxAcceleration, liftoff is achieved
    int belowAccelTime = 0;
    int maxBelowAccelTime = 6;
    float liftoffErrorFactor = -0.74;//-0.76
    float liftoffMaxErrorFactor = 1.05;//0.9;//1.1;
    float liftoffErrorConstant = 0;
    float landingDetectionFactor = 0.8;
    float landingErrorFactor = 0;//-0.3;
    float landingErrorConstant = 0;
    float recoverDetectionConstant = -0.5;
    unsigned long resetTime = 1100;

    // Physics parameters
    float velocity = 0;
    float displacement = 0;

    // Extrema values
    float maxVelocity = -999;
    float minVelocity = 999;
    float maxAccel = -999;
    float minDisplacement = 999;
    int timeSinceMax = 0;
    int timeSinceMin = 0;
    int timeSinceMaxAccel = 0;
    int timeSinceMinDisplacement = 0;
    int extremaDelta = 1;

    bool maxVelocitySet = false;

    float powerJumpDutyCycle = -.5;
    float powerJumpDriveDuration = 100;
    float lastPredUpdate = 0;

    unsigned long deltaTime = 0;

    /** Initiate VescUart class */
    VescUart UART;

    float current = 1.0; /** The current in amps */
    float currentBrake = 20.0;

    int firstDrive = 0;

    unsigned long lastPrint = 0;

    String driveStatus = "none";

    boolean powerJump = false;
    String powerJumpPhase = "none";

    // Light command
    bool lightCommandOn = false;

  private:
    void resetJumpStatus();
    static void isrA();
    static void isrB();
};

#endif
